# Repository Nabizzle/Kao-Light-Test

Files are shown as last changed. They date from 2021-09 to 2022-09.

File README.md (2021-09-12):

# Kao-Light-Test
Scripts for working with the Kao Light Test Model and Hardware

# Table of Contents

* [Getting Started](#getting-started)
  * [Prerequisites](#prerequisites)
* [Running the Code](#running-the-code)
* [Author](#author)
* [Description of Each Script](#description-of-each-script)
  * [panTiltModel.m](#pantiltmodelm)
  
  # Getting Started
  
  As of right now, there is only the modeling code, [panTIltModel.m](#pantiltmodelm), which makes a model of how the laser is controlled. In the future, the code for controlling the Arduino Uno to tilting and panning the read laser mount will be added.
  
  Also included are the Eagle files for making the shield for the Arduino that controlls the servos of the laser mount.
  
  ## Prerequisites
  
  Software:
  
  * [MATLAB 2018 or later](https://www.mathworks.com/help/matlab/) (For the computational model and prefinding tilt and pan angles)
  * [Arduino IDE](https://www.arduino.cc/en/software)
  
  Testing electronics (what is needed is based on the test)
  * Grapevine with micro D to Sub-D cable
  * [Arduino Uno](https://store-usa.arduino.cc/products/arduino-uno-rev3)
  * Arduino Uno Shield
  
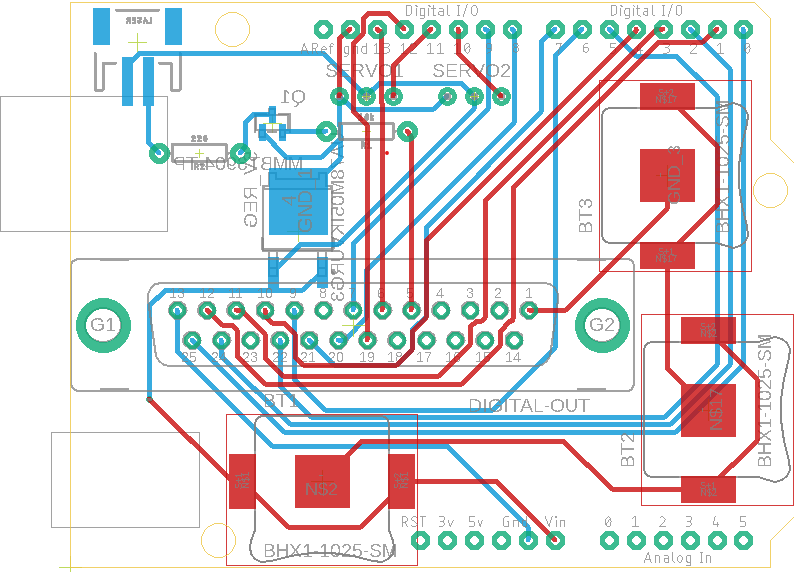
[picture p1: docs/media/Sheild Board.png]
Image of Shield Board
  
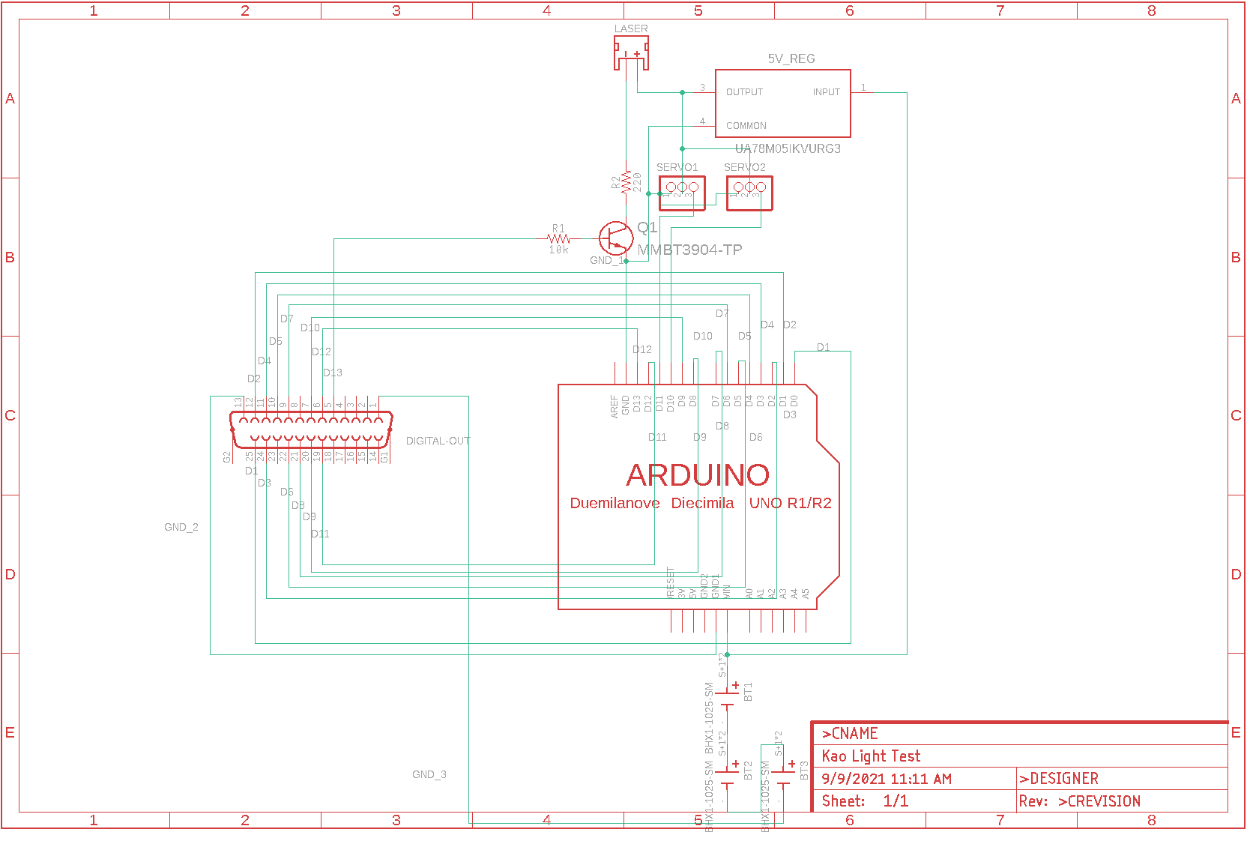
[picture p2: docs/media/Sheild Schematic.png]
Image of Shield Schematic
  
  
  # Running the Code
  
  When the Arduino code is added, you will need to plug in the shield and the servos and upload the Arduino code to it. You will also need to take the found tilt and pan angles for the grid size that you want and add them to the arduino code. Make sure that there are 4096 tilt values in a single row array.
  Also make sure to plug in the digital output cable from the Grapevine to the shield. This cable sends out the 12 bit digital signal to control for the 4096 angle values and a 13th signal to turn the laser on or off.
  
  # Author

  * **Nabeel Chowdhury** - Initial Creator
  
  # Description of Each Script
  
  ## panTiltModel.m
  Creates a computational model of the laser mount with user definable dimensions. For more information on how the model is made, refer to [this](https://github.com/Nabizzle/Kao-Light-Test/blob/main/docs/supplimentary/Modeling%20Laser%20Mount%20Pan%20and%20Tilt.pdf) supplimentary document.
  The code has 3 modes: debug, finding tilt and pan angles for a grid of points, visualizing the laser hit location of a given command position.
  
  In bebug mode, the laser tries to hit a square grid of points that is as wide as the gird is far away from the laser mount. The distance the mount is from the grid is user definable. The result of the laser mount hitting a 20x20 grid when 200 mm away from the grid is shown below.
  
  The finding angles mode, the user define a recangular grid of points for the model to find tile and pan angles for. This mode also outputs the expected laser hit locations for you to make sure that the code is working correctly.
  
  The final model allows you to set a command position at the top of the code and see that the model is hitting the right grid point.
  
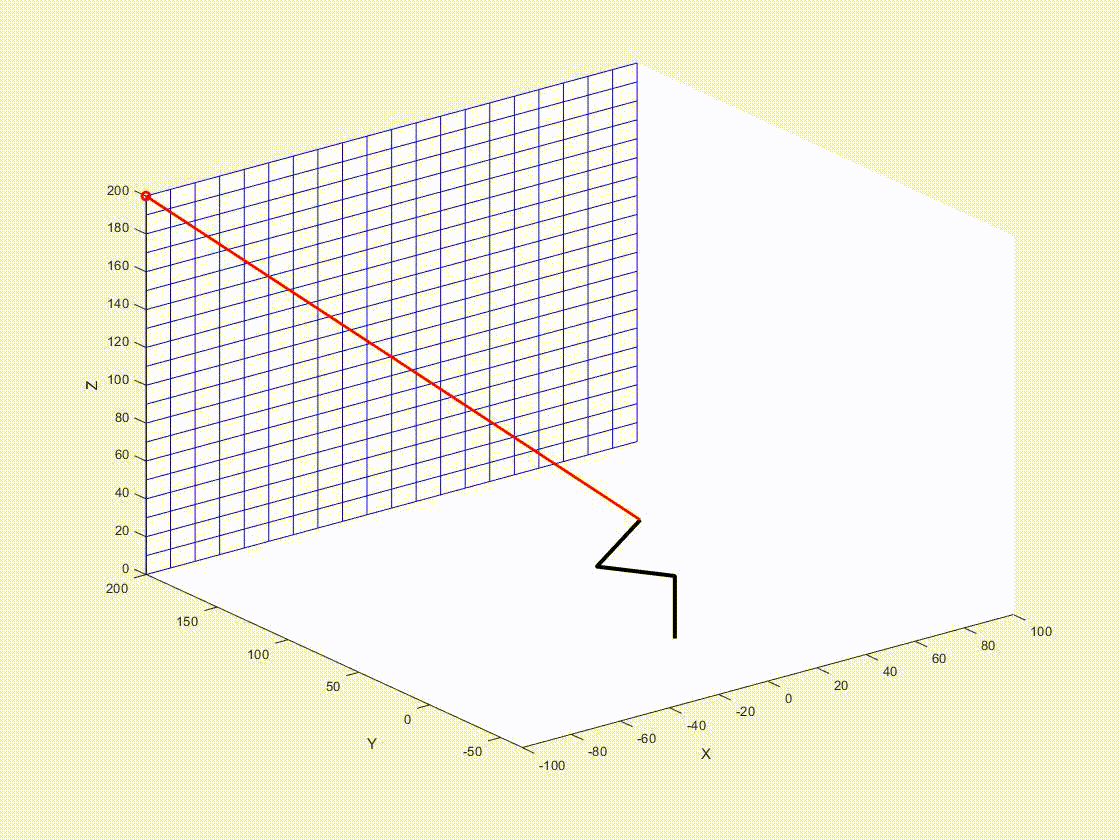
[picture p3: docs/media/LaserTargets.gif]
GIF of Debug Mode


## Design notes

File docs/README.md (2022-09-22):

# Kao-Light-Test
The Kao Light Test repository involves a set of scripts and an app used to analyze a subjects ownership of their peripersonal space. In order to do this, the experimenter selects positions for a laser to shine at various distances along or past the subject's arm. The subject is asked to react to the presence of the light as fast as possible by pressing on a foot pedal. The laser is aimed at the arm using two servos to pan and tilt the laser. The pan and tilt angles are commanded by the Grapevine NIP through 12 digital inputs (7 for 128 pan angles and 5 for 32 tilt angles.) The pan and tilt angles are centered around 90 degrees on each servo. There is also a model to calculate how the two servos should move to hit a user defined grid of points found in the [panTiltModel.m](#pantiltmodelm) script. This model can give an estimate of angles you want to use, but bear in mind that mapping to a flat grid will not be accurate to the curved surface of an arm.

 In the setup GUI, the experimenter chooses a list of pan and tilt angles for the test and the full list is repeated a user defined number of times and randomized. The servos will move at a random time before the laser shines so that the subject does not know when the laser will turn on.

# Table of Contents

* [Getting Started](#getting-started)
  * [Prerequisites](#prerequisites)
* [Running the Code](#running-the-code)
  * [Arduino Setup](#arduino-setup)
  * [Grapevine Setup](#grapevine-setup)
* [Running the Computational Model](#running-the-computational-model)
* [Author](#author)
* [Description of Each Script](#description-of-each-script)
  * [dataScrape.m](datascrapem)
  * [digitalOutputDebug.m](digitaloutputdebugm)
  * [footPedalDebug.m](footpedaldebugm)
  * [kaoLightTest.mlapp](kaolighttestmlapp)
  * [Kao_Light_Test.ino](kao_light_testino)
  * [laserDebug.ino](laserdebugino)
  * [laserStateWaveScrape.m](laserstatewavescrapemm)
  * [panTiltModel.m](#pantiltmodelm)
  
  # Getting Started
  
  Before running the full experiment on any given day, run the [footPedalDebug.m](#footpedaldebugm) to check that the foot pedal is working and the data is recording and run the [digitalOutputDebug.m](#digitaloutputdebugm) to check that the laser state indicator is recording.
  
  When starting to run the full test, open the [kaoLightTest.mlapp](kaolighttestmlapp) app which controls everything for the test. The app allows you to set pan and tilt angles that are sent to the arduino, toggle the laser on and off, sweep through the laser positions to check where on the arm the laser will be hitting, set the number of repeats of each point, and run the test.
  
  Before running the test, make sure all laser positions are visible to the subject.
  
  Also included in the repository are the Eagle files for making the shield for the Arduino that controls the servos of the laser mount.
  
  ## Prerequisites
  
  Software:
  
  * [MATLAB 2018 or later](https://www.mathworks.com/help/matlab/) (For the computational model)
  * [MATLAB 2020 or later](https://www.mathworks.com/help/matlab/) (For the MatLab app and debugging scripts)
  * [Arduino IDE](https://www.arduino.cc/en/software)
  
  Testing electronics (what is needed is based on the test)
  * Grapevine with micro D to Sub-D cable
  * [Arduino Uno](https://store-usa.arduino.cc/products/arduino-uno-rev3)
  * Arduino Uno PCB Shield
  
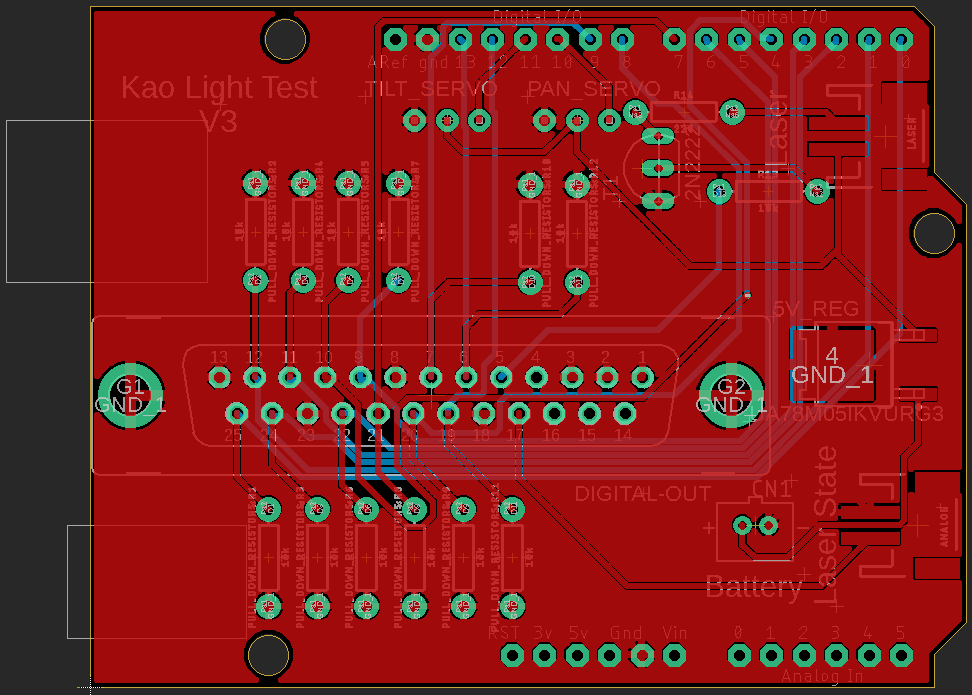
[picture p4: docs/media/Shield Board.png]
Image of Shield Board
  
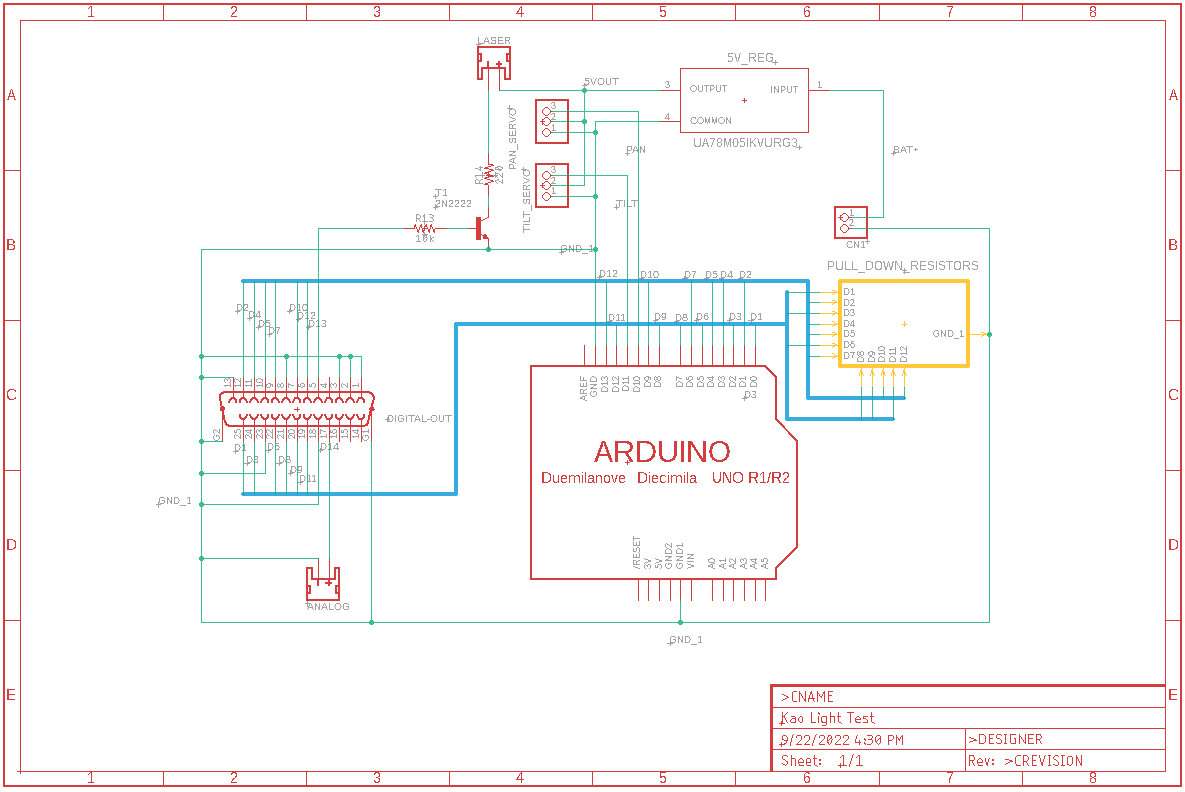
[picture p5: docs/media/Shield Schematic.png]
Image of Shield Schematic
  
  
  # Running the Code
  
  ## Arduino Setup
  
  Plug in the panning servo to signal pin 10 and the tilting servo to signal pin 11. **Note on older PCB's that in the image of the PCB these are labelled as servo 2 and servo 1 respectively, but in the current PCB, these servos are labelled as what angle they change. If the PCB is reprinted, then this note should be deleted.** Make sure that the 7.8 V LiPo battery is also plugged in and check that the laser is not on automatically. If it is, you may need to adjust the shield or check that the laser connector is not touching metal. Plug in the USB cable to the Arduino to power it.
  
  Make sure to plug in the digital output cable from the Grapevine to the shield. This cable sends out the 12 bit digital signal to control for the 4096 possible angle values (128 for panning and 32 for tilting), a 13th signal to turn the laser on or off, and a fourteenth for signalling to an analog input when the laser was turned on for matching to the foot pedal data.

  **Note that when uploading or reuploading a script to the arduino, you must disconnect the shield. The pull-down resistors on digital inputs 0 and 1 prevent the upload process from occurring.**
  
  ## Grapevine Setup
  
  Connect the foot pedal to a 5V supply or a 9 volt to a voltage regulator. Connect the foot switch so that when it is pressed, it sends a signal to the first SMA analog input. The laser indicator JST on the arduino shield to the second analog SMA input.

  # Running the Computational Model

  Open the [panTiltModel.m](#pantiltmodelm), which makes a model of how the laser could be controlled to hit a grid of points. Run this code to calculate the panning and tilting servo angles to hit this grid. The model allows you to define the size of the grid and the number of points that make up the grid. Bear in mind that while the model allows you to make an infinite grid of infinite points, the number of points actually feasible is limited by the small memory of the Arduino Uno.

  The code for the model allows for calculating the grid hits and has a debug mode that shows you an animation of the hits.
  
  # Author

  * **Nabeel Chowdhury** - Initial Creator of code and hardware.
  
  # Description of Each Script
  
  ## dataScrape.m
  This is the main data analysis script. It takes in the laser state and test angle indices to find where the tests occurred and then find the moment the foot pedal was first pressed to find a reaction time. For simplicity of data collection, it would make sense to be consistent the order of angles found, either proximal to distal or vise versa. Finally, the code outputs a figure to show the reaction times from proximal to distal on the arm.
  
  ## digitalOutputDebug.m
  This is a debug script for the laser state digital output. It starts recording for half a second, turns the laser indicator digital output on for half a second, and turns it off for half a second. Then the script outputs the recording from the second analog SMA input connection for you to verify the laser state indicator was recorded.
  
  ## footPedalDebug.m
  This is a debug script for the foot pedal. The script records through the first analog SMA input for 10 seconds and outputs the plot of the recordings live on the screen. Press the foot pedal to verify that the recording is occurring correctly.
  
  ## kaoLightTest.mlapp
  This is the main app for the test. The app has various functions described below.
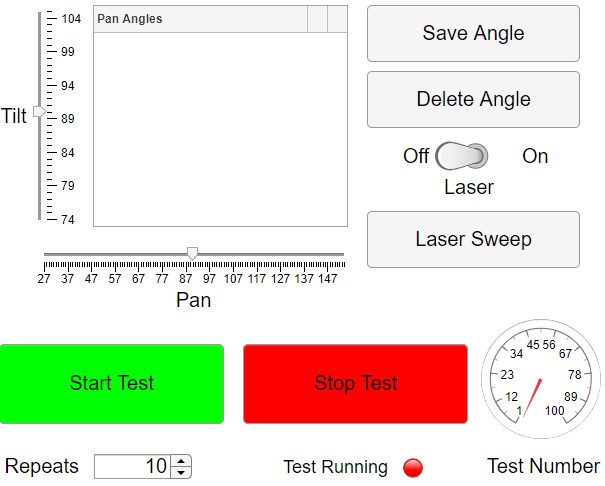
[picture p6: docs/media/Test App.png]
Image of Testing App
  
  
  The top of the app allows you to change the pan and tilt angles of the servos. Save the angles to the table next to the sliders by clicking the "Save Angle" button. When the angles are saved, the digital output is also displayed in the table for the experimenter to check. You can also select either the pan or tilt angle and edit it. When selecting an entry on the table, the servo will move to the position on that row of the table for you to check again. While an entry is selected, you can also delete it from the list with the "Delete Angle" button. Toggle the laser on or off with the laser toggle switch. When you have one or more saved angles, you can use the "Laser Sweep" button to move through all of the angles. 
  
  In the bottom of the app, there are start and stop buttons for the test to run the main experiment. This section also allows the experimenter to set the number of repeats of each angle. The main test duplicates the selected angles by the given number of repeats and randomizes the whole test array. The servos will move before the test begins and then after a 1-4 second delay, the laser will turn on. The subject then presses the foot pedal to react to the laser. The voltage across the foot pedal and the laser state digital output are recorded simultaneously. At the end of the test, the recording of the foot pedal recording, the laser state recordings, and the indices of the servo angles list is outputted to time stamped log files.
  
  ## Kao_Light_Test.ino
   The 12 digital inputs separated into a seven digit binary number for panning angles and a 5 digit binary number for tilt angles. These numbers are then converted to their base 10 equivalent and are added to an offset angle move the servos to their equivalent positions. The pan servo ranges from 27 to 154 degrees and the tilt servo ranges from 74 to 105 degrees.
  
  ## laserStateWaveScrape.m
  Takes in the laser state and targets arrays to find the times of the tests. Outputs a figure to show the found test timing as well as an array of each test time with the servo array index.
  
  ## panTiltModel.m
  Creates a computational model of the laser mount with user definable dimensions. For more information on how the model is made, refer to [this](https://github.com/iSensTeam/Kao-Light-Test/blob/main/docs/supplimentary/Modeling%20Laser%20Mount%20Pan%20and%20Tilt.pdf) supplementary document.
  The code has 3 modes: debug, finding tilt and pan angles for a grid of points, visualizing the laser hit location of a given command position.
  
  In debug mode, the laser tries to hit a square grid of points that is as wide as the gird is far away from the laser mount. The distance the mount is from the grid is user definable. The result of the laser mount hitting a 20x20 grid when 200 mm away from the grid is shown below.
  
  The finding angles mode, the user define a recangular grid of points for the model to find tile and pan angles for. This mode also outputs the expected laser hit locations for you to make sure that the code is working correctly.
  
  The final model allows you to set a command position at the top of the code and see that the model is hitting the right grid point.
  
  GIF of Debug Mode

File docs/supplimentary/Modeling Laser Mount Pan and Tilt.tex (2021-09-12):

\documentclass[12pt, letterpaper]{article}

\usepackage[utf8]{inputenc}
\usepackage{graphicx}
\usepackage{parskip}
\usepackage{amsmath}
\usepackage{amssymb}
\usepackage[section]{placeins}
\usepackage{import}
\usepackage{xifthen}
\usepackage{pdfpages}
\usepackage{transparent}
\usepackage{gensymb}

\graphicspath{{../media/}}

\title{Modeling Pan and Tilt of Laser Mount}
\author{Nabeel Chowdhury}
\date{\today}

\newcommand{\incfig}[1]{%
    \def\svgwidth{\columnwidth}
    \import{../media/}{#1.pdf_tex}
}

\begin{document}
	\maketitle
	\newpage
	
	\section{Description of Laser Mount Measurements}
		\begin{figure}[ht]
			\centering
			\resizebox{0.58\textwidth}{!}{\incfig{LaserMountDiagram}}
			\caption{\textbf{A} is the height of the panning arm and \textbf{$\theta_1$} is the rotation of the panning arm. \textbf{B} is the offset distance of the tilting arm. It is perpendicular to the panning arm. \textbf{C} is the length of the tilting arm. \textbf{D} is the distance of the base of the tilting arm to the target. This distance changes with panning angle, but stays constant with tilt.}
		\end{figure}
	
	\newpage
	\section{Finding Tilt Angle}
		\subsection{Laser Hit above A and Below Horizontal}
			\begin{figure}[ht]
				\centering
				\resizebox{0.7\textwidth}{!}{\incfig{Shallow Obtuse}}
				\caption{\textbf{D} is target's distance from the base of the tilting arm. \textbf{E} is the height above the base of the tilting arm that the laser hits its target. \textbf{a} is the hypotenuse of the extended triangle from the extrapolated intersection of the laser with the level of the base of the tilting arm. \textbf{b} is the hypotenuse of the extended triangle minus the distance of the base of the tilting arm to the target.}
			\end{figure}
			
			\newpage
			In order to find the height of the height of the target hit location, \textbf{E}, we need to find \textbf{b}.
			
			\begin{flalign*}
				b &= a-D &\\
				a &= \frac{C}{\sin(\theta_2 - 90 \degree)} = \frac{C}{-\cos(\theta_2)} &\\
				\therefore b &= -\frac{C}{\cos(\theta_2)} + D &\\
				-\frac{\textbf{E}}{\frac{C}{\cos(\theta_2)} + D} &= \tan(\theta_2 - 90 \degree) = -\cot(\theta_2)&\\
				\therefore \textbf{E} &= \left[D + \frac{C}{\cos(\theta_2)} \right] \cot(\theta_2) = D \cot(\theta_2) + \frac{C}{\sin(\theta_2)}&\\
			\end{flalign*}
			
			Now assuming we want to input in a target height to hit, we need to extract $\theta_2$ from the equation.
			
			\begin{flalign*}
				\text{If } x &= \tan(\frac{\theta_2}{2})\text{, } \sin(\theta_2) = \frac{2x}{1 + x^2}\text{, } \cos(\theta_2) = \frac{1 - x^2}{1 + x^2}\text{, } \tan(\theta_2) = \frac{2x}{1-x^2}&\\
				\textbf{E} &= D \frac{1-x^2}{2x} + C \frac{1 + x^2}{2x} &\\
				2\textbf{E}x &= D (1-x^2) + C (1 + x^2) &\\
				0 &= \left(C - D \right) x^2 - 2\textbf{E}x + C + D &\\
				x &= \frac{2\textbf{E} \pm \sqrt{4\textbf{E}^2 - 4\left( C - D \right)}}{2 \left( C - D \right)} = \tan(\frac{\theta_2}{2}) &\\
				&\therefore \boxed{\theta_2 = 2 \tan^{-1} \left[ \frac{2\textbf{E} \pm \sqrt{4\textbf{E}^2 - 4\left( C - D \right)}}{2 \left( C - D \right)} \right]} &\\
			\end{flalign*}
			
			The actual value of $\theta_2$ is the positive angle that results from the inverse tangent calculation.
			
		\subsection{Laser Hit above A and Above Horizontal}
			\begin{figure}[ht]
				\centering
				\resizebox{0.7\textwidth}{!}{\incfig{Acute}}
				\caption{\textbf{D} is target's distance from the base of the tilting arm. \textbf{E} is the height above the base of the tilting arm that the laser hits its target. \textbf{a} is the hypotenuse of the smaller extended triangle from the extrapolated intersection of the laser with the level of the base of the tilting arm.}
			\end{figure}
			
			In order to find $\theta_2$, we first need to find \textbf{E}.
			\begin{flalign*}
				a &= \frac{C}{\cos(\theta_2)} &\\
				\therefore \textbf{E} & = \frac{D + a}{\tan(\theta_2)} = \frac{D + \frac{C}{\cos(\theta_2)}}{\tan(\theta_2}&\\
				\textbf{E} &= D \cot(\theta_2) + \frac{C}{\sin(\theta_2)}&\\
			\end{flalign*}
			
			This is the same result as the previous calculation. Therefore,
			\begin{flalign*}
				\theta_2 = 2 \tan^{-1} \left[ \frac{2\textbf{E} \pm \sqrt{4\textbf{E}^2 - 4\left( C - D \right)}}{2 \left( C - D \right)} \right]
			\end{flalign*}
			
		\subsection{Laser Hit below A}
			\begin{figure}[ht]
				\centering
				\resizebox{0.58\textwidth}{!}{\incfig{Deep Obtuse}}
				\caption{\textbf{D} is target's distance from the base of the tilting arm. \textbf{E} is the height below the base of the tilting arm that the laser hits its target. \textbf{a} is the distance from the base of the tilting arm to where the laser crosses the horitontal axis with respect to the base of the tilting arm. It is also the hypotenuse of the triangle made by the tilting arm and the laser crossing the horizontal made by the base of the tilting arm. \textbf{b} is the distance from the crossing to the target wall.}
			\end{figure}
			
			\newpage
			Once again, we need to find \textbf{E} based on the tilt angle.
			\begin{flalign*}
				b &= D - a &\\
				a &= \frac{C}{\cos(180 \degree - \theta_2)} = -\frac{C}{\cos(\theta_2)}&\\
				\textbf{E} &= \frac{b}{\tan(180 \degree - \theta_2)} = \frac{D + \frac{C}{\cos(\theta_2)}}{\tan(180 \degree - \theta_2)} = -\frac{\frac{C}{\cos(\theta_2)} + D}{\tan(\theta_2)} &\\
				\textbf{E} &= -\frac{C}{\sin(\theta_2)} - D \cot(\theta_2) &\\
			\end{flalign*}
			
			Solving for $\theta_2$:
			\begin{flalign*}
				\text{If } x &= \tan(\frac{\theta_2}{2})\text{, } \sin(\theta_2) = \frac{2x}{1 + x^2}\text{, } \cos(\theta_2) = \frac{1 - x^2}{1 + x^2}\text{, } \tan(\theta_2) = \frac{2x}{1-x^2}&\\
				\textbf{E} &= -C \frac{1 + x^2}{2x} - D \frac{1-x^2}{2x}&\\
				2\textbf{E}x &= -C (1 + x^2) - D (1-x^2)&\\
				0 &= \left(C - D \right) x^2 + 2\textbf{E}x + C + D &\\
			\end{flalign*}
			
			If we define E as negative when below the horizontal made by the base of the tilting arm, we get the same result as previously where.
				\begin{flalign*}
				\theta_2 = 2 \tan^{-1} \left[ \frac{2\textbf{E} \pm \sqrt{4\textbf{E}^2 - 4\left( C - D \right)}}{2 \left( C - D \right)} \right]
			\end{flalign*}
	
	\newpage		
	\section{Finding Pan Angle}
		\begin{figure}[ht]
			\centering
			\resizebox{0.9\textwidth}{!}{\incfig{Pan}}
			\caption{\textbf{B} is the length of the base of the tilting arm. \textbf{D} is target's distance from the base of the tilting arm. \textbf{F} horizontal distance of the target from center. \textbf{G} is the target's perpendicular distance from the panning arm.}
		\end{figure}
		
		Solving for $\theta_1$:
		\begin{flalign*}
			\tan(\theta_1) &= \frac{F}{G} &\\
			& \boxed{\therefore \theta_1 = \tan^{-1}(\frac{F}{G})} &\\
		\end{flalign*}
			
		\textbf{D} is a different distance now that the arm has panned. To find the new distance of D needed in the tilt angle calculations, we do the following:
		\begin{flalign*}
			\cos(\theta_1) &= \frac{G}{D + B} &\\
			D &= \frac{G}{\cos(\theta_1)} - B &\\
		\end{flalign*}
		
	\section{Creating a Model of the Laser Mount}
		\subsection{Creating the Default Position}
			In order to model how the tilt and pan angles will affect laser placement on the target and to debug issues while excluding hardware issues, I made a virtual model of the laser mount.
			
			Each segment of the model is oriented along the z axis first and then the pan and tilt local angles are applied. The angles between the base of the tilt arm and the pan arm and the laser with the tilt arm are set as $-90 \degree$.
			
			In this position, the pan angle turns the laser to the left and a positive tilt angle is subtracted from $180 \degree$. In the default position shown below, the tilt angle is $90 \degree$.
			
			\begin{figure}[ht]
				\centering
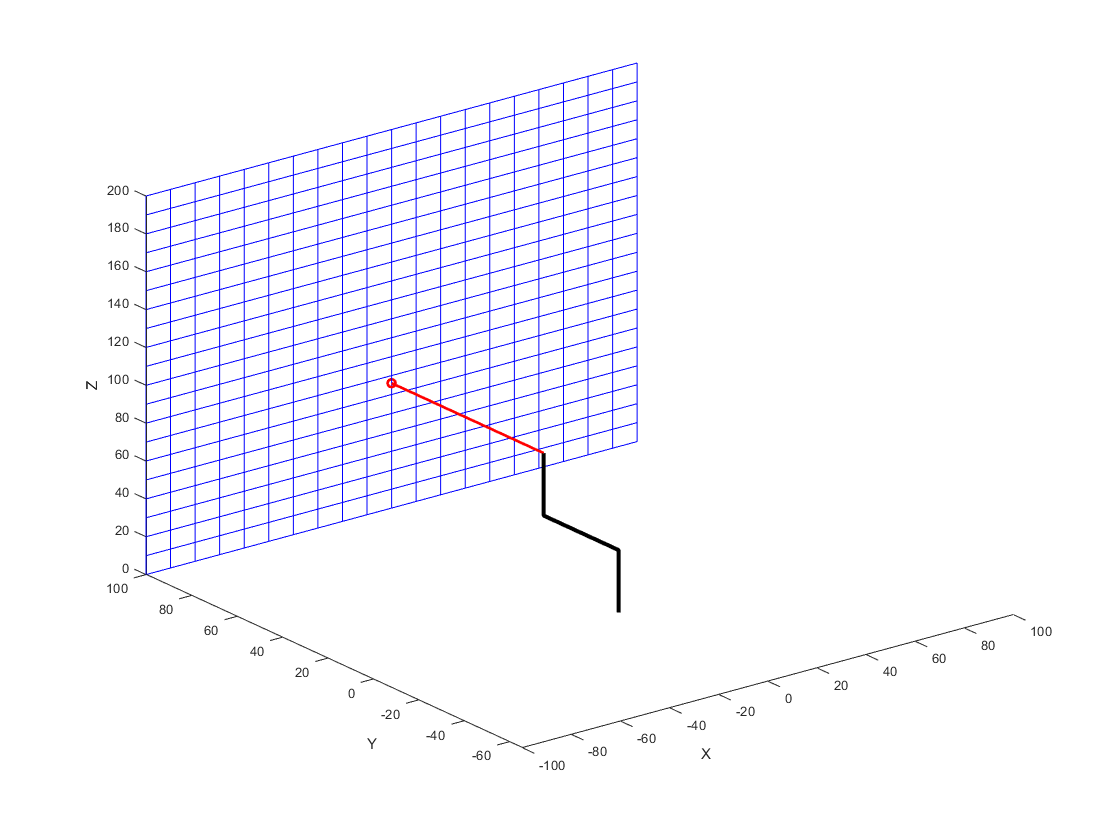
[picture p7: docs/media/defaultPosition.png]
				\resizebox{0.9\textwidth}{!}{}
				\caption{The default position of the laser mount.}
			\end{figure}
		
		\subsection{Applying Local Rotations}
			When applying the tilt and pan angles, they need to be applied as local rotations and converted to the global positioning of the points that define the laser mount.
			\subsubsection{Rotation Matrices}
				The rotation matrices are below:
				
				\textbf{Rotation About the X Axis}
				\begin{equation*}
				R_x = 
					\begin{bmatrix}
						&1 &0 &0 \\
    					&0 &\cos(\theta) &\sin(\theta) \\
    					&0 &-\sin(\theta) &\cos(\theta)
					\end{bmatrix}
				\end{equation*}
				
				\textbf{Rotation About the Y Axis}
				\begin{equation*}
				R_y = 
					\begin{bmatrix}
						&\cos(\theta) &0 &-\sin(\theta) \\
    					&0 &1 &0 \\ 
    					&\sin(\theta) &0 &\cos(\theta)
					\end{bmatrix}
				\end{equation*}
				
				\textbf{Rotation About the Z Axis}
				\begin{equation*}
				R_z = 
					\begin{bmatrix}
						&\cos(\theta) &\sin(\theta)&0 \\
    					&\-sin(\theta) &\cos(\theta) &0 \\
    					&0 &0 &1
					\end{bmatrix}
				\end{equation*}
			
			\subsubsection{Matrix Multiplication}
				Matrix multiplication is done starting from the origin, which is the base of the panning arm, and then working out towards the each point of the mount to the end of the laser. Each new rotation is applied to the left of the previous rotations. The rotated location of each point is found by inverting the combined rotation matrices and multiplying it by the length of the segment. The new point then needs to be translated by the value of the previous point. 
				
				\textbf{Rotating the Panning Arm}
				\begin{flalign*}
					\begin{bmatrix}
						&x_P \\
						&y_P \\
						&z_P
					\end{bmatrix} &= R_z^{-1}(\theta_1)					
					\begin{bmatrix}
						&0 \\
						&0 \\
						&A
					\end{bmatrix} &\\
				\end{flalign*}
				
				\textit{Note that this rotation will always return the same position as the panning arm is align along the z axis at the origin.}
				
				\textbf{Rotating the Base of the Tilt Arm}
				\begin{flalign*}
					\begin{bmatrix}
						&x_B \\
						&y_B \\
						&z_B
					\end{bmatrix} &= (R_x(-90 \degree) R_z(\theta_1))^{-1}				
					\begin{bmatrix}
						&0 \\
						&0 \\
						&B
					\end{bmatrix} + 
					\begin{bmatrix}
						&x_P \\
						&y_P \\
						&z_P
					\end{bmatrix} &\\
				\end{flalign*}		
				
				\textbf{Rotation of the Tilt Arm}
				\begin{flalign*}
					\begin{bmatrix}
						&x_T \\
						&y_T \\
						&z_T
					\end{bmatrix} &= (R_x(\theta_2)R_x(-90 \degree) R_z(\theta_1))^{-1}				
					\begin{bmatrix}
						&0 \\
						&0 \\
						&C
					\end{bmatrix} +
					\begin{bmatrix}
						&x_B \\
						&y_B \\
						&z_B
					\end{bmatrix} &\\
				\end{flalign*}
				
				\textbf{Laser Hit Location}
				\begin{flalign*}
					\text{Laser Length} &= L = \frac{D + \frac{C}{\cos(\theta_2)}}{\sin(\theta_2) - C\tan(\theta_2)} &\\					
					\text{if } \theta_2 &= 90 \degree \text{, }L=D &\\
					\begin{bmatrix}
						&x_L \\
						&y_L \\
						&z_L
					\end{bmatrix} &= (R_x(-90 \degree)R_x(\theta_2)R_x(-90 \degree) R_z(\theta_1))^{-1}				
					\begin{bmatrix}
						&0 \\
						&0 \\
						&L
					\end{bmatrix} +
					\begin{bmatrix}
						&x_T \\
						&y_T \\
						&z_T
					\end{bmatrix} &\\
				\end{flalign*}
				
				The length of the laser found about is the distance from the laser diode to the wall.
\end{document}

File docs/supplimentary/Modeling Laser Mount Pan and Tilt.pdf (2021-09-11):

# Modeling Pan and Tilt of Laser Mount

### Nabeel Chowdhury

### September 11, 2021

1

## 1 Description of Laser Mount Measurements

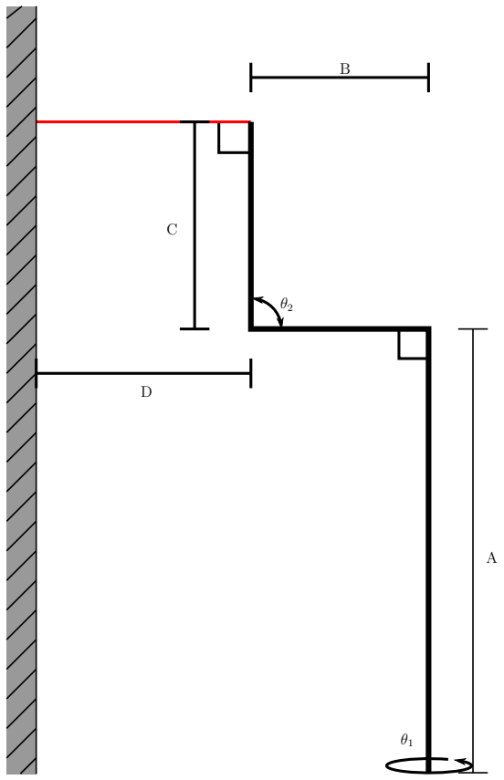
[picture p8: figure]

Figure 1: A is the height of the panning arm and θ1 is the rotation of the panning arm. B is the offset distance of the tilting arm. It is perpendicular to the panning arm. C is the length of the tilting arm. D is the distance of the base of the tilting arm to the target. This distance changes with panning angle, but stays constant with tilt.

2

## 2 Finding Tilt Angle

### 2.a Laser Hit above A and Below Horizontal

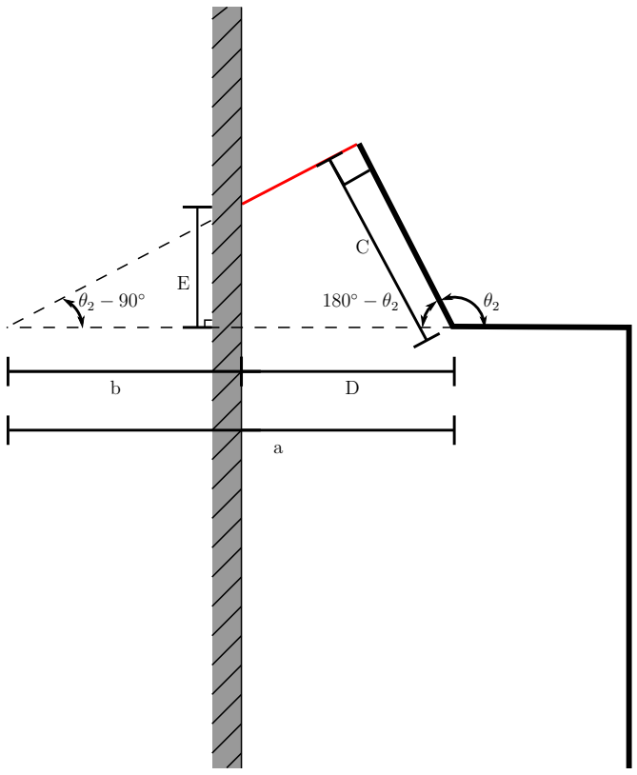
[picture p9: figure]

Figure 2: D is target’s distance from the base of the tilting arm. E is the height above the base of the tilting arm that the laser hits its target. a is the hypotenuse of the extended triangle from the extrapolated intersection of the laser with the level of the base of the tilting arm. b is the hypotenuse of the extended triangle minus the distance of the base of the tilting arm to the target.

3

In order to find the height of the height of the target hit location, E, we need to find b.

b = a − D

a =

C
sin(θ2 − 90◦
)

=

C
− cos(θ2)

∴ b = −

C
cos(θ2)

+ D

−

E

C
cos(θ2) + D

= tan(θ2 − 90◦
) = − cot(θ2)

∴ E =

D +

C
cos(θ2)
cot(θ2) = D cot(θ2) + C sin(θ2)

Now assuming we want to input in a target height to hit, we need to extract θ2 from the equation.

If x = tan(θ2
2

), sin(θ2) = 2x
1 + x

2

, cos(θ2) = 1 − x

2
1 + x

2

, tan(θ2) = 2x
1 − x

2

E = D

1 − x

2
2x

+ C

1 + x

2
2x
2Ex = D(1 − x

2
) + C(1 + x

2
)
0 = (C − D) x

2 − 2Ex + C + D

x =

2E ±

p
4E

2 − 4 (C − D)
2 (C − D)

= tan(θ2
2

)

∴ θ2 = 2 tan⁻¹

"
2E ±

p
4E

2 − 4 (C − D)
2 (C − D)

The actual value of θ2 is the positive angle that results from the inverse tangent calculation.

4

### 2.b Laser Hit above A and Above Horizontal

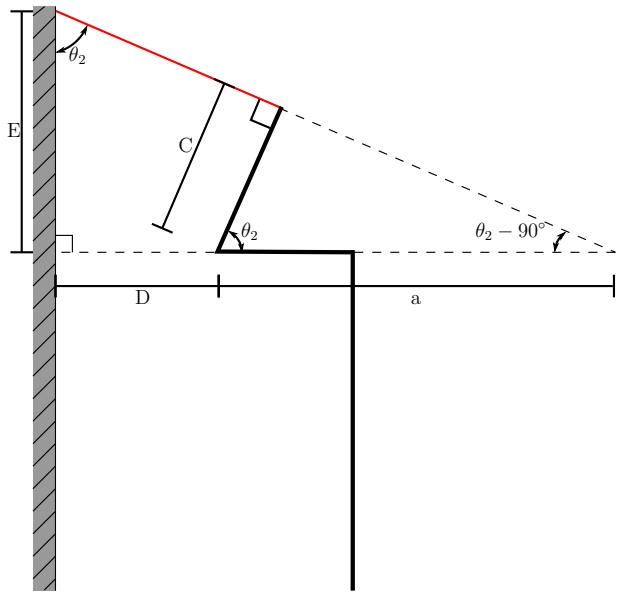
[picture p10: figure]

Figure 3: D is target’s distance from the base of the tilting arm. E is the height above the base of the tilting arm that the laser hits its target. a is the hypotenuse of the smaller extended triangle from the extrapolated intersection of the laser with the level of the base of the tilting arm.

In order to find θ2, we first need to find E.

a =

C
cos(θ2)

∴ E =

D + a
tan(θ2)

=

D +

C
cos(θ2)
tan(θ2
E = D cot(θ2) + | C
| sin(θ2)

This is the same result as the previous calculation. Therefore,

θ2 = 2 tan⁻¹

"
2E ±

p
4E

2 − 4 (C − D)
2 (C − D)

5

### 2.c Laser Hit below A

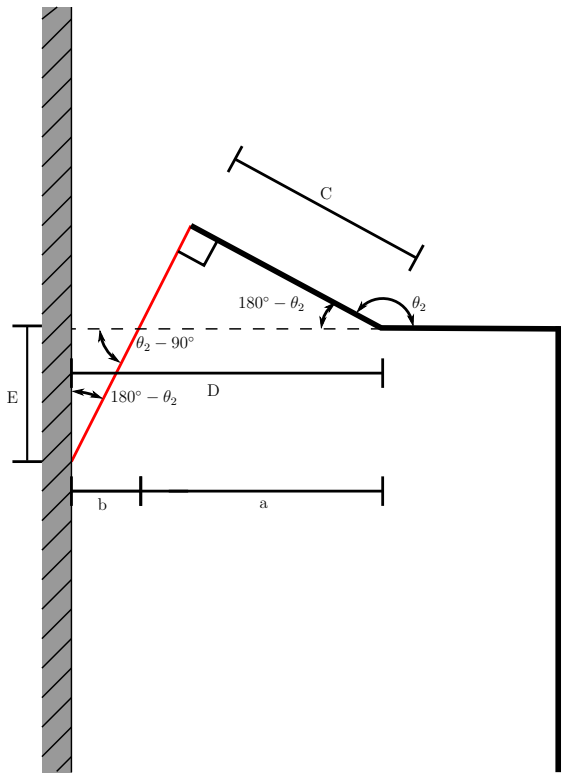
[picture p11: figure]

Figure 4: D is target’s distance from the base of the tilting arm. E is the height below the base of the tilting arm that the laser hits its target. a is the distance from the base of the tilting arm to where the laser crosses the horitontal axis with respect to the base of the tilting arm. It is also the hypotenuse of the triangle made by the tilting arm and the laser crossing the horizontal made by the base of the tilting arm. b is the distance from the crossing to the target wall.

6

Once again, we need to find E based on the tilt angle.

b = D − a

a =

C
cos(180◦ − θ2)

= −

C
cos(θ2)

E =

b
tan(180◦ − θ2)

=

D +

C
cos(θ2)
tan(180◦ − θ2)

= −

C
cos(θ2) + D
tan(θ2)

E = −

C
sin(θ2)

− D cot(θ2)

Solving for θ2:

If x = tan(θ2
2

), sin(θ2) = 2x
1 + x

2

, cos(θ2) = 1 − x

2
1 + x

2

, tan(θ2) = 2x
1 − x

2

E = −C

1 + x

2
2x

− D

1 − x

2
2x
2Ex = −C(1 + x

2
) − D(1 − x

2
)
0 = (C − D) x

2 + 2Ex + C + D

If we define E as negative when below the horizontal made by the base of the tilting arm, we get the same result as previously where.

θ2 = 2 tan⁻¹

"
2E ±

p
4E

2 − 4 (C − D)
2 (C − D)

7

## 3 Finding Pan Angle

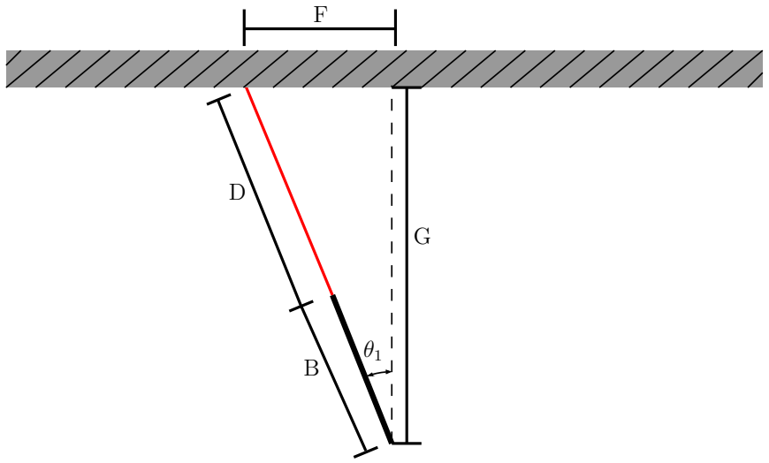
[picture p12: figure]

Figure 5: B is the length of the base of the tilting arm. D is target’s distance from the base of the tilting arm. F horizontal distance of the target from center. G is the target’s perpendicular distance from the panning arm.

Solving for θ1:

tan(θ1) = F
G

∴ θ1 = tan⁻¹
(

F
G

)

D is a different distance now that the arm has panned. To find the new distance of D needed in the tilt angle calculations, we do the following:

cos(θ1) = | G D + B
D = | G cos(θ1)
− B

8

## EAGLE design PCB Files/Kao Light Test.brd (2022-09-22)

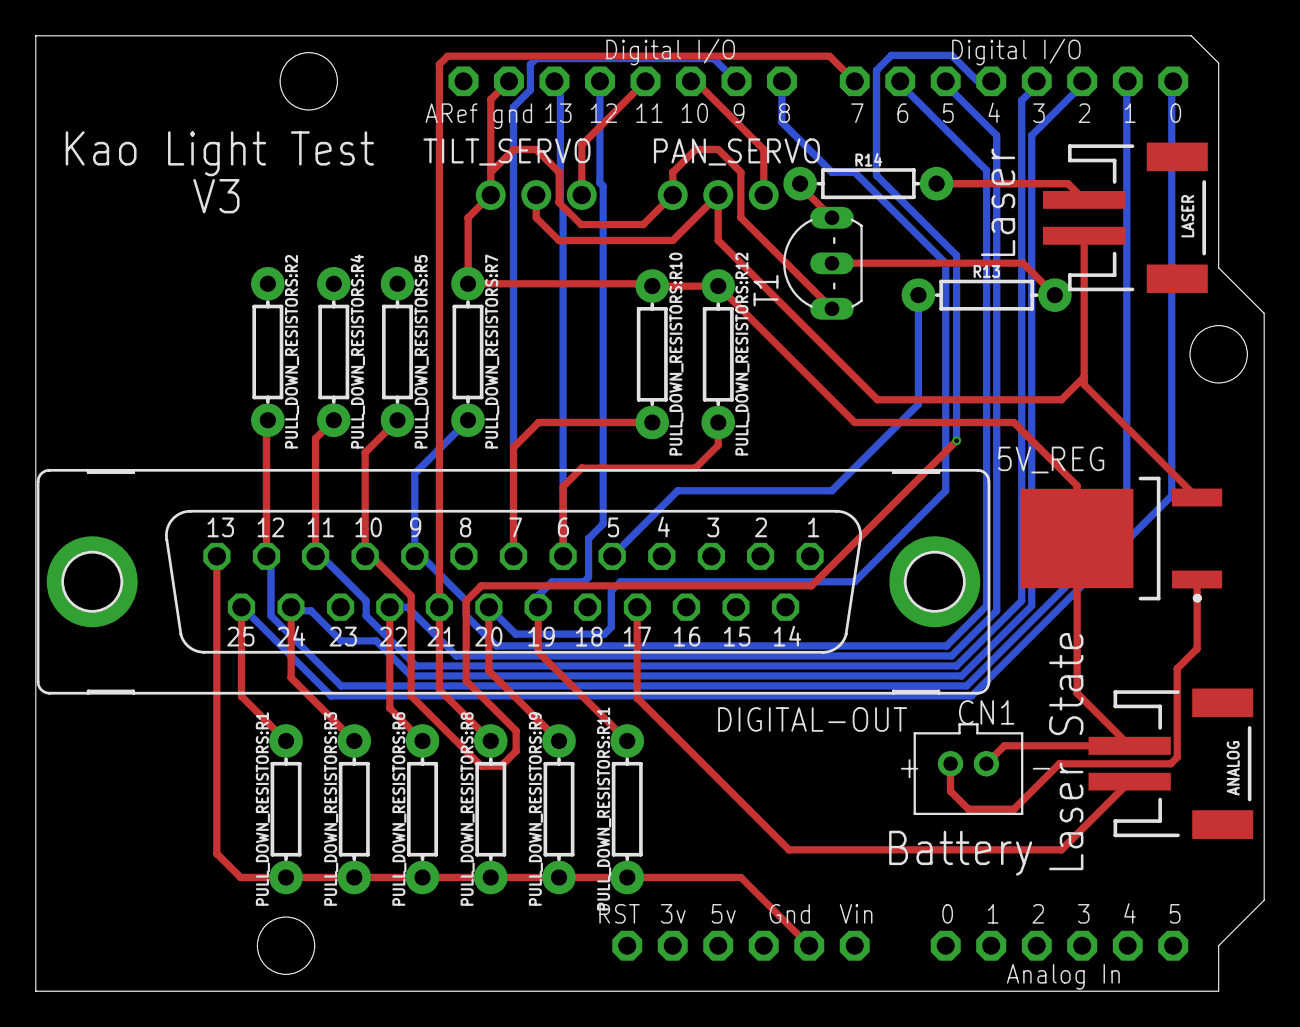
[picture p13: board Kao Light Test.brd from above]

Board: 2 copper layers, 68.6 x 53.3 mm, 23 parts (0 on the bottom side), 22 nets.

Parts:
5V_REG: UA78M05IKVURG3; KVU0003A_N
ANALOG: JST-2-SMD
CN1: JST-PH-2-THM
DIGITAL-OUT: F25VP
LASER: JST-2-SMD
PAN_SERVO: 1X03-CLEANBIG
PULL_DOWN_RESISTORS:R1, PULL_DOWN_RESISTORS:R2, PULL_DOWN_RESISTORS:R3, PULL_DOWN_RESISTORS:R4, PULL_DOWN_RESISTORS:R5, PULL_DOWN_RESISTORS:R6, PULL_DOWN_RESISTORS:R7, PULL_DOWN_RESISTORS:R8, PULL_DOWN_RESISTORS:R9, PULL_DOWN_RESISTORS:R10, PULL_DOWN_RESISTORS:R11, PULL_DOWN_RESISTORS:R12: 10k; AXIAL-0.3
R13: 10k; AXIAL-0.3
R14: 220; AXIAL-0.3
T1: 2N2222; TO92-EBC-OVAL
TILT_SERVO: 1X03-CLEANBIG
U$1: ARDUINOUNO; ARDUINO

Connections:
5VOUT: 5V_REG.3, LASER.2, PAN_SERVO.2, TILT_SERVO.2
BAT+: 5V_REG.1, CN1.1
D1: DIGITAL-OUT.25, PULL_DOWN_RESISTORS:R1.P$2, U$1.D0
D2: DIGITAL-OUT.12, PULL_DOWN_RESISTORS:R2.P$2, U$1.D1
D3: DIGITAL-OUT.24, PULL_DOWN_RESISTORS:R3.P$2, U$1.D2
D4: DIGITAL-OUT.11, PULL_DOWN_RESISTORS:R4.P$2, U$1.D3
D5: DIGITAL-OUT.10, PULL_DOWN_RESISTORS:R5.P$2, U$1.D4
D6: DIGITAL-OUT.22, PULL_DOWN_RESISTORS:R6.P$2, U$1.D5
D7: DIGITAL-OUT.9, PULL_DOWN_RESISTORS:R7.P$2, U$1.D6
D8: DIGITAL-OUT.21, PULL_DOWN_RESISTORS:R8.P$2, U$1.D7
D9: DIGITAL-OUT.20, PULL_DOWN_RESISTORS:R9.P$2, U$1.D8
D10: DIGITAL-OUT.7, PULL_DOWN_RESISTORS:R10.P$2, U$1.D9
D11: DIGITAL-OUT.19, PULL_DOWN_RESISTORS:R11.P$2, U$1.D12
D12: DIGITAL-OUT.6, PULL_DOWN_RESISTORS:R12.P$2, U$1.D13
D13: DIGITAL-OUT.5, R13.P$1
D14: ANALOG.2, DIGITAL-OUT.17
GND_1: 5V_REG.4, ANALOG.1, CN1.2, DIGITAL-OUT.1, DIGITAL-OUT.2, DIGITAL-OUT.3, DIGITAL-OUT.8, DIGITAL-OUT.13, DIGITAL-OUT.18, DIGITAL-OUT.23, DIGITAL-OUT.G1, DIGITAL-OUT.G2, PAN_SERVO.1, PULL_DOWN_RESISTORS:R1.P$1, PULL_DOWN_RESISTORS:R2.P$1, PULL_DOWN_RESISTORS:R3.P$1, PULL_DOWN_RESISTORS:R4.P$1, PULL_DOWN_RESISTORS:R5.P$1, PULL_DOWN_RESISTORS:R6.P$1, PULL_DOWN_RESISTORS:R7.P$1, PULL_DOWN_RESISTORS:R8.P$1, PULL_DOWN_RESISTORS:R9.P$1, PULL_DOWN_RESISTORS:R10.P$1, PULL_DOWN_RESISTORS:R11.P$1, PULL_DOWN_RESISTORS:R12.P$1, T1.E, TILT_SERVO.1, U$1.GND, U$1.GND1
unnamed: R13.P$2, T1.B
unnamed: R14.P$1, T1.C
unnamed: LASER.1, R14.P$2
PAN: PAN_SERVO.3, U$1.D10
TILT: TILT_SERVO.3, U$1.D11

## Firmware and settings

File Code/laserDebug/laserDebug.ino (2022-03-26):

//create the variables to store the digital output values
int dig_0 = 0;
int dig_1 = 0;
int dig_2 = 0;
int dig_3 = 0;
int dig_4 = 0;
int dig_5 = 0;
int dig_6 = 0;
int dig_7 = 0;
int dig_8 = 0;
int dig_9 = 0;
int dig_12 = 0;
int dig_13 = 0;
//store the value of the array index
int index = 0;
 
void setup() {
  //set digial pins 0-9 and 12-13 to input
  pinMode(0, INPUT);
  pinMode(1, INPUT);
  pinMode(2, INPUT);
  pinMode(3, INPUT);
  pinMode(4, INPUT);
  pinMode(5, INPUT);
  pinMode(6, INPUT);
  pinMode(7, INPUT);
  pinMode(8, INPUT);
  pinMode(9, INPUT);
  pinMode(12, INPUT);
  pinMode(13, INPUT);
  //start the serial monitor
  Serial.begin(9600);
}
void loop() {
  dig_0 = digitalRead(0);
  dig_1 = digitalRead(1);
  dig_2 = digitalRead(2);
  dig_3 = digitalRead(3);
  dig_4 = digitalRead(4);
  dig_5 = digitalRead(5);
  dig_6 = digitalRead(6);
  dig_7 = digitalRead(7);
  dig_8 = digitalRead(8);
  dig_9 = digitalRead(9);
  dig_12 = digitalRead(12);
  dig_13 = digitalRead(13);

  index = dig_0 + dig_1 * 2 + dig_2 * 4 + dig_3 * 8 + dig_4 * 16 + dig_5 * 32 + dig_6 * 64 + dig_7 * 128 + dig_8 * 256 + dig_9 * 512 + dig_12 * 1024 + dig_13 * 2048;
  
  Serial.print(index);
  Serial.print("\n");
}

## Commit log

2021-09-11 feat: Adds functionality to code that finds angles
    The code how finds angles for a 5mm rectangular grid and also has code
    that outputs the locations where the model expects the laser to hit the
    target.
2021-09-12 feat: Adds switch case to modes
    Eliminates the if else statements in favor of a switch statement. NOTE,
    there is still a bug in mode 2 for finidng angles
2021-09-12 docs: Adds Images of Arduino Shield
2021-09-12 docs: Adds an SVG file for the target grid
    The grid is colored in case you want to laser cut it and engrave the
    grid
2021-09-12 feat: Adds the Eagle files
    [Kao Light Test.brd, Kao Light Test.sch]
2022-03-26 feat: Convert the graph to volts
2022-03-26 feat: Adds script to convert digital signal to num
    Adds a debug script for finding the base 10 number from the input
    digital signals. NOTE that the first two outputs are always set to their
    values since they are also used for the serial monitor. They should work
    when commanding the servos.
    Closes #2
2022-03-26 fix: Changes the model to only have 400 points
    The lowered number of points to to account for the arduino's memory
2022-03-26 feat: Creates the script to control the servos
    Adds an arduino script to take in the digital outputs of the Grapevine
    and move the servo to desired positions based on the computational model
    Closes #7
2022-03-26 fix: Changes the model to fit the real dimensions
    Changes the model and the arrays of found positions to match the real
    dimensions of the testing setup
    [Kao_Light_Test.ino]
2022-03-26 feat: Creates app and servo angle finder function
    Crates the code to find the servo angles and lets the experimentor
    examine them. Also outputs the variables to the workspace in case the
    user wants to copy over the angles to the arduino.
    Closes #8
2022-03-26 feat: Adds a function to test the laser
    Adds a laser toggle and a function to determine where the laser will hit
    with its various tilt angles
2022-03-26 feat: Adds a function to pan the laser at tilt
    Adds a function to pan the laser at the current tilt angle.
    Closes #1
2022-03-28 feat: Adds Test stop and Validates code
    Adds a lamp to indicate when the test is running, a stop test button,
    and validates that all parts of the test work at least without a
    subject. The code also now saves out the servo angles used for the test
    which it needed to previously, but I forgot to add.
    Closes #10
2022-03-28 fix: Turns on the laser in the laser sweep code
    The laser did not actually turn on in the laser sweep code. Also
    shortens the time between each pan angle in the laser sweep.
2022-03-29 fix: Addresses error in the main test
    The laser didn't turn on in the test since the laser state indicator
    would turn off the parallel port. Now, both turn on together.
2022-09-15 feat: Saves a list of test angles
    App now allows the user to save a list of tilt angles for the test as
    well as manually edit or delete elements of the list. The current code
    allows duplicate entries, but that could be eliminated if undesired.
    Closes #14 issue.
2022-09-19 feat: updates PCB
    Adds changes from Issue #9
    [Kao Light Test.brd, Kao Light Test.sch]
2022-09-19 BREAKING CHANGE feat: Grapevine to controls angle
    Changes code so that the first seven digital outputs of the Grapevine
    control the pan angle of the laser and the last 5 digital outputs
    control the tilt angle. The rest of the functions are updated
    accordingly. For example all code to calculate angles was been deleted
    and the functions that refered to the calculated angles have been
    updated to use the new angle formats. Also added a Guage for test
    number. Also accomplishes much of issues #13
    Closes #15 issue, Closes #17 issue
2022-09-19 feat: Updates the look of the GUI
    Makes the laser toggle a toggle switch and updates the start button
    color
2022-09-20 feat: Grapevine controls pan and tilt angles
    The arduino takes the 12 digital inputs from the Grapevine and converts
    the first 7 into 128 different pan angles and the last 5 inputs as 32
    different tilt angles. The pan and tilt angles range around the center
    of their range of motion.
    Closes #11 and closes #13 issues.
    [Kao_Light_Test.ino]
2022-09-21 chore: Updates the code for new laser state output
    Switches the output from the first SMA to the 14th output of the microD
    connector
2022-09-21 feat: Improves the look of the PCB
    Improves the naming and clenliness of the PCB
    [Kao Light Test.brd, Kao Light Test.sch]
2022-09-21 docs: Updates the ReadMe with the new PCB design.
2022-09-21 docs: Adds name of test to PCB
    [Kao Light Test.brd]
2022-09-21 feat: Grounds the Cable's housing.
    Also updates the images in the ReadMe
    [Kao Light Test.brd, Kao Light Test.sch]
2022-09-22 docs: Adds note to the ReadMe on flashing scripts
    Adds a note that the arduino shield must be disconnected from the
    arduino when flashing a new script as the pull-down resistors on digital
    inputs 0 and 1 prevent the upload process from occurring. This is also
    why the Serial monitor does not work properly with the shield for these
    pins.
2022-09-22 docs: Updates the PCB and ReadMe to be clearer
    The PCB was updated so that the servos are labeled as what they are
    instead of as numbers. One resistor was also updated and all other
    digital grounds were connected to the ground plane.
    [Kao Light Test.brd, Kao Light Test.sch]
2022-09-22 fix: Corrects logic in code
    Corrects how the arduino interprets digital inputs from the grapevine.
    [Kao_Light_Test.ino]
2022-09-22 feat: Tests and corrects errors in test
    Tests the code on the Grapevine. Testing revealed that the resistor
    connected between the laser and the transistor's collector needed to be
    the original value of 220 ohms and all of the pull-down resistors need
    to be at least 10k Ohms or higher.
2022-09-22 docs: Updates PCB and ReadMe based on testing
    Updates the PCB resistor values and images of the PCB based on the
    testing done in the previous commit.
    [Kao Light Test.brd, Kao Light Test.sch]

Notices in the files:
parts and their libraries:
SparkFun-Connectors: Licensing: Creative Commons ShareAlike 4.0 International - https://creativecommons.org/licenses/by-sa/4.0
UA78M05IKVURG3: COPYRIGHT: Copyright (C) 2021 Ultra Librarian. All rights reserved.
